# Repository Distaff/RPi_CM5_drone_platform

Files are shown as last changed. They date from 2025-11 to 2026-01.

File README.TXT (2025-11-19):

These files have been created in version 9 of KiCAD.

Some of the 3d models need to be downloaded form the following places and put into the CM5IO.3shapes directory some models are approximations.

https://datasheets.raspberrypi.org/cm5/CM5-step.zip
https://www.molex.com/molex/products/part-detail/memory_card_socket/5033981892

The models provided in the 3dmodels directory are from various manufacturers including Diodes, Hirose, MTCONN, Toby, TRXCOM. Terms and conditions for the use of the models remain with the original manufacture.

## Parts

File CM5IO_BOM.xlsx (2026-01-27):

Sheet: Bottom
Qty/ board | Ref | Value | Footprint | Desc | Part No. | MOUSER |  | Farnell |  | TME
 |  |  |  |  |  | Unit Price | Code | Unit Price | Code | Unit Price | Code | min. Il. na 10 płytek
4 | C9,C12,C13,C18 | 100n | Capacitor_SMD:C_0402_1005Metric | 0.1uF 10% 16V Ceramic Capacitor X7R 0402 (1005 Metric) | - |  |  |  |  | 0.04 zł | 04025C104KAT2A (https://www.tme.eu/pl/details/04025c104kat2a/kondensatory-mlcc-smd/kyocera-avx/) | 12 | 0.47 zł
1 | CP6 | 33pF | Capacitor_SMD:C_0805_2012Metric_Pad1.18x1.45mm_HandSolder | - | - |  |  |  |  | 0.20 zł | 08055A330KAT2A (https://www.tme.eu/pl/details/08055a330kat2a/kondensatory-mlcc-smd/kyocera-avx/) | 12 | 2.46 zł
1 | CP5 | 2.7nF | Capacitor_SMD:C_0805_2012Metric_Pad1.18x1.45mm_HandSolder | - | - |  |  |  |  | 0.18 zł | 08055C272KAT2A (https://www.tme.eu/pl/details/08055c272kat2a/kondensatory-mlcc-smd/kyocera-avx/) | 12 | 2.19 zł
1 | CP7 | 10nF | Capacitor_SMD:C_0805_2012Metric_Pad1.18x1.45mm_HandSolder | - | - |  |  |  |  | 0.14 zł | 08055C103KAT2A (https://www.tme.eu/pl/details/08055c103kat2a/kondensatory-mlcc-smd/kyocera-avx/) | 12 | 1.71 zł
1 | CP4 | 100nF | Capacitor_SMD:C_0805_2012Metric_Pad1.18x1.45mm_HandSolder | - | - |  |  |  |  | 0.04 zł | 08055C104KAT2A (https://www.tme.eu/pl/details/08055c104kat2a/kondensatory-mlcc-smd/kyocera-avx/) | 12 | 0.50 zł
4 | C2,C5,C7,C8 | 10u | Capacitor_SMD:C_0805_2012Metric | 10uF 10% 10V Ceramic Capacitor X7R 0805 (2012 Metric) | - |  |  |  |  | 0.28 zł | 08055C105KAT2A (https://www.tme.eu/pl/details/08055c105kat2a/kondensatory-mlcc-smd/kyocera-avx/) | 42 | 11.85 zł
3 | R1,R2,R10 | 1k | Resistor_SMD:R_0402_1005Metric | Resistor 1K M1005 1% 63mW | - |  |  |  |  | 0.03 zł | SMD0402-1K-1% (https://www.tme.eu/pl/details/smd0402-1k-1%25/rezystory-smd/royalohm-royal-electronic-fty-co/0402wgf1001tce/) | 100 | 3.31 zł
4 | R6,R7,R8,R9 | 2.2K 1% | Resistor_SMD:R_0402_1005Metric | Resistor 2.2K M1005 1% 63mW | - |  |  |  |  | 0.04 zł | SMD0402-2K2-1% (https://www.tme.eu/pl/details/smd0402-2k2-1%25/rezystory-smd/royalohm-royal-electronic-fty-co/0402wgf2201tce/) | 100 | 3.91 zł
2 | R11,R13 | 10K 1% | Resistor_SMD:R_0402_1005Metric | Resistor 10K M1005 1% 63mW | - |  |  |  |  | 0.02 zł | SMD0402-10K-1% (https://www.tme.eu/pl/details/smd0402-10k-1%25/rezystory-smd/royalohm-royal-electronic-fty-co/0402wgf1002tce/) | 100 | 1.76 zł
1 | R12 | 15K 1% | Resistor_SMD:R_0402_1005Metric | Resistor 15K M1005 1% 63mW | - |  |  |  |  | 0.04 zł | SMD0402-15K-1% (https://www.tme.eu/pl/details/smd0402-15k-1%25/rezystory-smd/royalohm-royal-electronic-fty-co/0402wgf1502tce/) | 100 | 3.66 zł
1 | RP1 | 115K | Resistor_SMD:R_0805_2012Metric_Pad1.20x1.40mm_HandSolder | - | - |  |  |  |  | 0.22 zł | ERA6AEB1153V (https://www.tme.eu/pl/details/era6aeb1153v/rezystory-smd/panasonic-industry-europe-gmbh/) | 12 | 2.59 zł
1 | RP2 | 22.1K | Resistor_SMD:R_0805_2012Metric_Pad1.20x1.40mm_HandSolder | - | - |  |  |  |  | 0.06 zł | SMD0805-22K1-1% (https://www.tme.eu/pl/details/smd0805-22k1-1%25/rezystory-smd/royalohm-royal-electronic-fty-co/0805s8f2212t5e/) | 100 | 5.94 zł
1 | RP3 | 15.8K | Resistor_SMD:R_0805_2012Metric_Pad1.20x1.40mm_HandSolder | - | - |  |  |  |  | 0.07 zł | SMD0805-15.8K-1% (https://www.tme.eu/pl/details/smd0805-15.8k-1%25/rezystory-smd/royalohm-royal-electronic-fty-co/0805s8f1582t5e/) | 100 | 6.71 zł
1 | J1 | POWER TERMINAL | TerminalBlock:TerminalBlock_bornier-2_P5.08mm | - | -
1 | J2 | Conn_02x06_Odd_Even | Connector_PinHeader_2.00mm:PinHeader_2x06_P2.00mm_Vertical | PinHeader_2x06_P2.54mm_Vertical | -
1 | J4 | J_PSU_EN | Connector_PinHeader_2.54mm:PinHeader_1x02_P2.54mm_Vertical | - | -
1 | J8 | THD-20-R | Connector_PinHeader_2.54mm:PinHeader_2x20_P2.54mm_Vertical | PinHeader_2x20_P2.54mm_Vertical | THD-20-R
 |  |  |  |  |  |  |  |  |  |  |  | SUMA | 47.04 zł
1 | CP1 | 10uF | Capacitor_Tantalum_SMD:CP_EIA-3528-21_Kemet-B_HandSolder | Tantalum, Kemet-B, 10uF@35V min. | - |  |  |  |  | 0.00 zł | -
2 | CP2,CP3 | 22uF | Capacitor_Tantalum_SMD:CP_EIA-3528-21_Kemet-B_HandSolder | Tantalum, Kemet-B, 22uF@10V min. | - |  |  |  |  | 1.64 zł | TAJB226K016R (https://www.tme.eu/pl/details/tajb226k016r/kondensatory-tantalowe-smd/kyocera-avx/tajb226k016rnj/)
1 | C3 | 100uF | Capacitor_Tantalum_SMD:CP_EIA-7343-31_Kemet-D | Kemet-D, 10V | - |  |  |  |  | 2.28 zł | TAJD106K035R (https://www.tme.eu/pl/details/tajd106k035r/kondensatory-tantalowe-smd/kyocera-avx/tajd106k035rnj/)
2 | D1,D3 | LED Red | LED_SMD:LED_0603_1608Metric | Red 620nm LED Indication - Discrete 2.2V 2-SMD, No Lead | SML-A12U8TT86Q |  |  | 1.65 zł | 3434715 (https://pl.farnell.com/rohm/sml-a12u8tt86/led-red-63mcd-620nm/dp/3434715) | 0.00 zł | -
1 | D2 | LED Green | LED_SMD:LED_0603_1608Metric | Green 572nm LED Indication - Discrete 2.2V 2-SMD, No Lead | SML-A12M8TT86N |  |  | 1.64 zł | 3434712 (https://pl.farnell.com/rohm/sml-a12m8tt86/led-yellow-green-25mcd-572nm/dp/3434712) | 0.00 zł | -
2 | J5,J16 | Conn_01x22_Female | CM5IO:Hirose_FH12-22S-0.5SH_1x22-1MP_P0.50mm_Horizontal | 22 Position FFC, FPC Connector Contacts, Bottom 0.020" (0.50mm) Surface Mount, Right Angle | FH12-22S-0.5SH55 |  |  | 7.17 zł | 2300373 (https://pl.farnell.com/hirose-hrs/fh12-22s-1sh-55/connector-fpc-ffc-smt-1mm-22way/dp/2300373) | 0.00 zł | -
1 | J7 | Micro_SD_Card_Det | CM5IO:SDCARD_MOLEX_503398-1892 | 9 (8 + 1) Position Card Connector microSDâ„¢ Surface Mount, Right Angle Gold | 503398-1892 |  |  |  |  | 8.41 zł | MX-503398-1892 (https://www.tme.eu/pl/details/mx-503398-1892/zlacza-do-kart/molex-interconnect-gmbh/503398-1892/) | Not necessary, if no SD card is used
1 | J11 | USB_C_Receptacle_USB2.0 | Connector_USB:USB_C_Receptacle_GCT_USB4105-xx-A_16P_TopMnt_Horizontal | USBC USB2 data and power connector | USBF31-0171 |  |  |  |  | 2.58 zł | UBC-RA-TF* (https://www.tme.eu/pl/details/ubc-ra-tf/zlacza-usb-i-ieee1394/jst-j-s-t-deutschland-gmbh/ubc-ra-tf-hf/) | * - equivalent
1 | J12 | USB3_A | Connector_USB:USB3_A_Molex_48393-001 | USB 3.0 A connector | 48393-0003 |  |  |  |  | 9.67 zł | MX-48393-0003 (https://www.tme.eu/pl/details/mx-48393-0003/zlacza-usb-i-ieee1394/molex-interconnect-gmbh/48393-0003/)
1 | J14 | JST_SHBM04B-SRSS-TB | Connector_JST:JST_SH_BM04B-SRSS-TB_1x04-1MP_P1.00mm_Vertical | 4 pin vertical 1mm pitch connector | SHBM04B-SRSS-TB |  |  |  |  | 1.44 zł | SM04B-SRSS-TB (https://www.tme.eu/pl/details/sm04b-srss-tb/zlacza-sygnalowe-raster-1-00mm/jst-j-s-t-deutschland-gmbh/sm04b-srss-tb-lf-sn/)
1 | J22 | 46765-1301 | CM5IO:CONN_467651301_MOL | 0.40mm Pitch Micro HDMI Connector, Right-Angle Receptacle, Surface Mount, with Through Hole Shell Tabs and Pick-and-Place Polyimide Tape, 19 Circuits, Lead-Free | 46765-1301 |  |  | 8.82 zł | 2614867 (https://pl.farnell.com/molex/46765-1301/hdmi-connector-rcpt-19pos-smt/dp/2614867) | 0.00 zł | -
1 | LP1 | 3.6uH | Inductor_SMD:L_Bourns-SRN8040_8x8.15mm | - | SRN8040HA-3R6M |  |  | 2.52 zł | 4216300 (https://pl.farnell.com/bourns/srn8040ha-3r6m/power-inductor-3-6uh-semishielded/dp/4216300) | 0.00 zł | -
2 | Module1 | ComputeModule5-CM5 | CM5IO:Raspberry-Pi-5-Compute-Module | 100 Position Connector Receptacle, Center Strip Contacts Surface Mount Gold | 10164227-1001A1RLF | 0.00 zł | - | 7.43 zł | 4137104 (https://pl.farnell.com/amphenol-communications-solutions/10164227-1001a1rlf/mezzanine-conn-rcpt-100pos-2row/dp/4137104) | 0.00 zł | -
1 | SW1 | Right angle Tact button | Button_Switch_SMD:SW_Push_1P1T_NO_CK_KMR2 | - | KMR221G LFS |  |  |  |  | 1.05 zł | KMR221GLFS (https://www.tme.eu/pl/details/kmr221glfs/mikroprzelaczniki-tact/c-k-components-sas/kmr221g-lfs/)
1 | U6 | AP22653W6 | Package_TO_SOT_SMD:SOT-23-6 | Power Switch/Driver 1:1 P-Channel 2.1A SOT-23-6 | AP22653W6 |  |  |  |  | 1.45 zł | AP22653W6-7 (https://www.tme.eu/pl/details/ap22653w6-7/power-switches-uklady-scalone/diodes-incorporated/)
1 | U12 | RT9742SNGV | Package_TO_SOT_SMD:TSOT-23_HandSoldering | Power Switch/Driver 1:1 N-Channel 500mA SOT-23-3 | RT9742SNGV |  |  | 1.50 zł | 2575555 (https://pl.farnell.com/richtek/rt9742sngv/uswi00154-rt9742sngv/dp/2575555) | 0.00 zł | -
1 | U18 | RT9742GGJ5 | Package_TO_SOT_SMD:SOT-23-5 | Power Switch/Driver 1:1 N-Channel 1A TSOT-23-5 | RT9742GGJ5 |  |  | 0.00 zł | - | 0.00 zł | - | Not necessary, if no SD card is used
1 | UP1 | AP64501SP-13 | CM5IO:SOP_AP64501SP-13_DIO | - | AP64501SP-13 |  |  |  |  | 7.11 zł | AP64501SP-13 (https://www.tme.eu/pl/details/ap64501sp-13/regulatory-napiecia-uklady-dc-dc/diodes-incorporated/)
 |  |  |  |  |  |  |  | 46.98 zł | SUMA / płytka | 37.27 zł | SUMA / płytka

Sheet: Top
Qty/ board | Ref | Value | Footprint | Desc | Part No. | MOUSER |  | Farnell |  | TME
 |  |  |  |  |  | Unit Price | Code | Unit Price | Code | Unit Price | Code | min. Il. na 10 płytek
1 | J8 | THD-20-R | Connector_PinHeader_2.54mm:PinHeader_2x20_P2.54mm_Vertical | TODO: to ma być gniazdo | - |  |  |  |  |  |  |  | 0.00 zł
1 | J3 | J_PSU_EN | Connector_PinHeader_2.54mm:PinHeader_1x02_P2.54mm_Vertical_SMD_Pin1Left | - | - |  |  |  |  |  |  |  | 0.00 zł
4 | C1,C2,C7,C8 | 470nF | Capacitor_SMD:C_0805_2012Metric_Pad1.18x1.45mm_HandSolder | - | - |  |  |  |  | 0.25 zł | 08055C474K4T2A (https://www.tme.eu/pl/details/08055c474k4t2a/kondensatory-mlcc-smd/kyocera-avx/) | 50 | 12.36 zł
10 | R1,R3,R4,R5,R6,R9,R10,R12,R13,R15 | 1K | Resistor_SMD:R_0805_2012Metric_Pad1.20x1.40mm_HandSolder | - | - |  |  |  |  | 0.05 zł | SMD0805-1K-1% (https://www.tme.eu/pl/details/smd0805-1k-1%25/rezystory-smd/royalohm-royal-electronic-fty-co/0805s8f1001t5e/) | 100 | 4.97 zł
1 | R2 | 2.2K 1% | Resistor_SMD:R_0805_2012Metric_Pad1.20x1.40mm_HandSolder | - | - |  |  |  |  | 0.06 zł | SMD0805-2K2-1% (https://www.tme.eu/pl/details/smd0805-2k2-1%25/rezystory-smd/royalohm-royal-electronic-fty-co/0805s8f2201t5e/) | 100 | 5.62 zł
2 | R7,R8 | 5.1K 1% | Resistor_SMD:R_0805_2012Metric_Pad1.20x1.40mm_HandSolder | - | - |  |  |  |  | 0.06 zł | SMD0805-5K1-1% (https://www.tme.eu/pl/details/smd0805-5k1-1%25/rezystory-smd/royalohm-royal-electronic-fty-co/0805s8f5101t5e/) | 100 | 5.94 zł
3 | R11,R14,R16 | 10K | Resistor_SMD:R_0805_2012Metric_Pad1.20x1.40mm_HandSolder | - | - |  |  |  |  | 0.05 zł | SMD0805-10K-1% (https://www.tme.eu/pl/details/smd0805-10k-1%25/rezystory-smd/royalohm-royal-electronic-fty-co/0805s8f1002t5e/) | 100 | 4.97 zł
 |  |  |  |  |  |  |  |  |  |  |  | SUMA/całość | 33.85 zł
2 | C3,C4 | 4.7uF 35v | Capacitor_Tantalum_SMD:CP_EIA-3528-21_Kemet-B_HandSolder | - | - |  |  |  |  | 1.68 zł | TAJB475K035R (https://www.tme.eu/pl/details/tajb475k035r/kondensatory-tantalowe-smd/kyocera-avx/tajb475k035rnj/)
2 | C5,C6 | 4.7uF 10v | Capacitor_Tantalum_SMD:CP_EIA-3216-18_Kemet-A_HandSolder | - | - |  |  |  |  | 1.48 zł | TAJA475K010R (https://www.tme.eu/pl/details/taja475k010r/kondensatory-tantalowe-smd/kyocera-avx/taja475k010rnj/)
2 | D1,D2 | MBR1020VL | Diode_SMD:D_SOD-123F | - | MBR1020VL |  |  |  |  | 0.98 zł | MBR1020VL-AU-R1 (https://www.tme.eu/pl/details/mbr1020vl-au-r1/diody-schottky-smd/panjit-semiconductor-panjit-international-inc/mbr1020vl-au-r1-000a1/)
2 | D3,D5 | LED Red | LED_SMD:LED_0603_1608Metric | Red 620nm LED Indication - Discrete 2.2V 2-SMD, No Lead | SML-A12U8TT86Q |  |  |  |  | 0.15 zł | LTST-C190KRKT* (https://www.tme.eu/pl/details/ltst-c190krkt/diody-led-smd-kolorowe/lite-on-technology/) | * - equivalent
1 | D4 | LED Green | LED_SMD:LED_0603_1608Metric | Green 572nm LED Indication - Discrete 2.2V 2-SMD, No Lead | SML-A12M8TT86N |  |  |  |  | 0.12 zł | LTST-C190KGKT* (https://www.tme.eu/pl/details/ltst-c190kgkt/diody-led-smd-kolorowe/lite-on-technology/)
1 | J1 | USB_C_Receptacle_USB2.0 | Connector_USB:USB_C_Receptacle_GCT_USB4105-xx-A_16P_TopMnt_Horizontal | - |  |  |  |  |  | 2.58 zł | UBC-RA-TF (https://www.tme.eu/pl/details/ubc-ra-tf/zlacza-usb-i-ieee1394/jst-j-s-t-deutschland-gmbh/ubc-ra-tf-hf/)
1 | J4 | J_ESP_DBG_UART | Connector_Molex:Molex_PicoBlade_53047-0210_1x02_P1.25mm_Vertical | - | 53047-0210 |  |  |  |  | 0.90 zł | MX-53047-0210 (https://www.tme.eu/pl/details/mx-53047-0210/zlacza-sygnalowe-raster-1-25mm/molex-interconnect-gmbh/53047-0210/)
1 | J7 | J_FC_UART | Connector_Molex:Molex_PicoBlade_53048-0210_1x02_P1.25mm_Horizontal | - | 53048-0210 |  |  |  |  | 0.93 zł | MX-53048-0210 (https://www.tme.eu/pl/details/mx-53048-0210/zlacza-sygnalowe-raster-1-25mm/molex-interconnect-gmbh/53048-0210/)
2 | J9,J10 |  | Connector_Molex:Molex_PicoBlade_53048-0810_1x08_P1.25mm_Horizontal | - | 53048-0810 |  |  |  |  | 2.25 zł | MX-53048-0810 (https://www.tme.eu/pl/details/mx-53048-0810/zlacza-sygnalowe-raster-1-25mm/molex-interconnect-gmbh/53048-0810/)
2 | Q1,Q4 | AO3401A | Package_TO_SOT_SMD:SOT-23 | - | AO3401A |  |  |  |  | 1.24 zł | AO3401A (https://www.tme.eu/pl/details/ao3401a/tranzystory-z-kanalem-p-smd/alpha-omega-semiconductor-inc/)
2 | Q2,Q3 | Q_NPN_BEC | Package_TO_SOT_SMD:SOT-23 | -
3 | SW1,SW2,SW3 |  | Button_Switch_SMD:SW_Push_1P1T_NO_CK_KMR2 | - | KMR221G LFS |  |  |  |  | 1.05 zł | KMR221GLFS (https://www.tme.eu/pl/details/kmr221glfs/mikroprzelaczniki-tact/c-k-components-sas/kmr221g-lfs/)
1 | U1 | ESP32-S3-WROOM-1 | RF_Module:ESP32-S3-WROOM-1U | - | ESP32-S3-WROOM-1 |  |  |  |  | 23.40 zł | ESP32S3-WRM1U-16R8 (https://www.tme.eu/pl/details/esp32s3-wrm1u-16r8/moduly-iot-wifi-bluetooth/espressif-systems/esp32-s3-wroom-1u-n16r8/)
1 | U2 | Wio-SX1262 | CM5IO_top:Wio-SX1262 | - | Seed Studio 114993390 |  |  |  |  | 0.00 zł | -
2 | U3,U4 | AP7361C-33E | Package_TO_SOT_SMD:SOT-223-3_TabPin2 | - | AP7361C-33E |  |  |  |  | 1.53 zł | AP7361C-33E-13 (https://www.tme.eu/pl/details/ap7361c-33e-13/stabilizatory-napiecia-nieregulowane-ldo/diodes-incorporated/)
 |  |  |  |  |  |  |  |  |  | 49.70 zł | SUMA / płytka

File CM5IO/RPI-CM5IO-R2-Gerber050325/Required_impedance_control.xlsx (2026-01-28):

Signal Layer | Reference Layer | Impedance Type | Trace Width（mil) | Trace Spacing（mil) | Impedance(ohm)±10% | Position
L1 | L2 | Differential Pair (Non coplanar) | 4.25 | 5.9055 | 100
L4 | L3 | Differential Pair (Non coplanar) | 4.25 | 5.9055 | 100
L1 | L2 | Differential Pair (Non coplanar) | 6.6 | 9.9606 | 90
L4 | L3 | Differential Pair (Non coplanar) | 6.6 | 9.9606 | 90

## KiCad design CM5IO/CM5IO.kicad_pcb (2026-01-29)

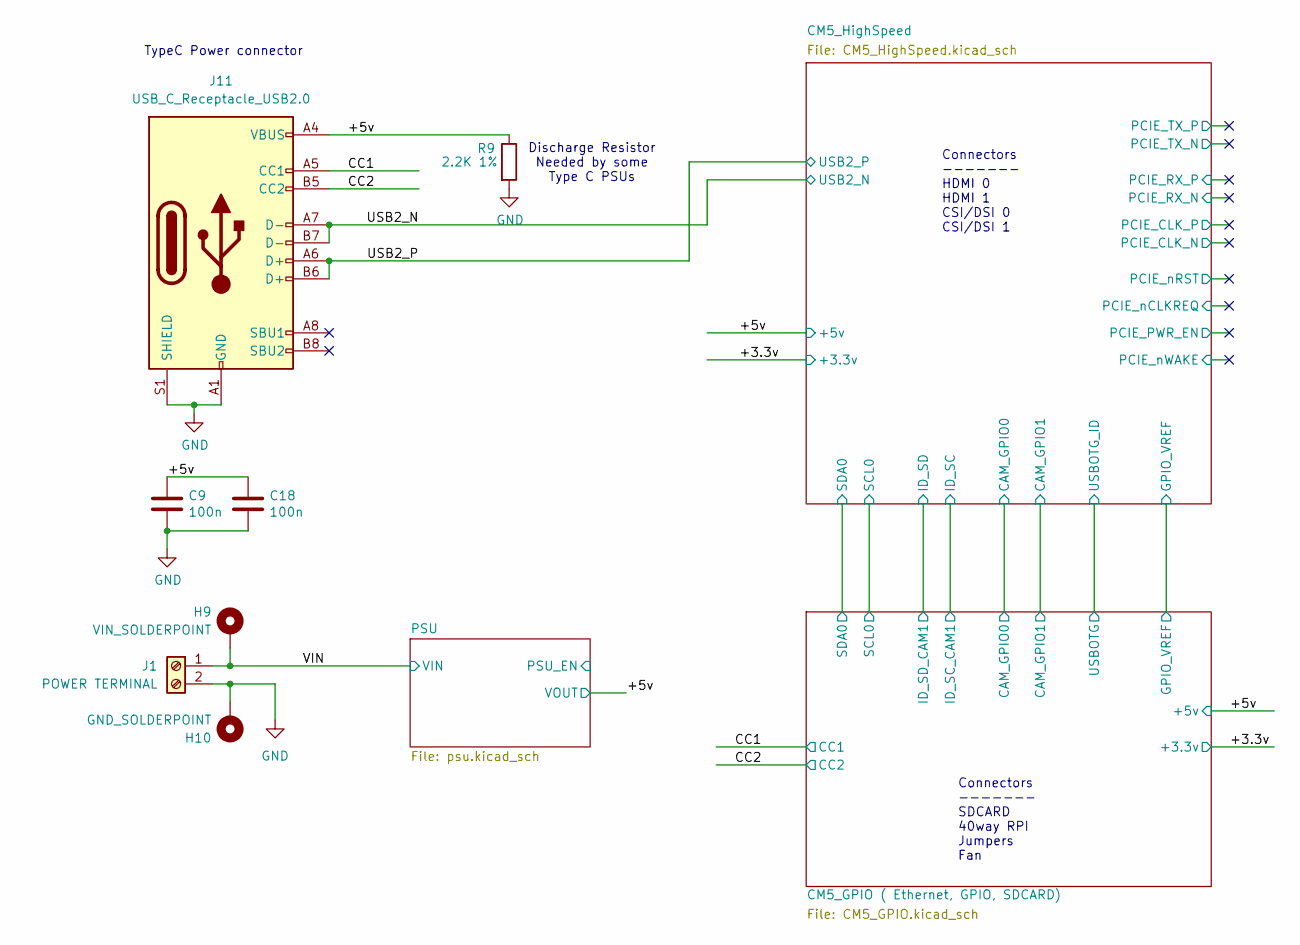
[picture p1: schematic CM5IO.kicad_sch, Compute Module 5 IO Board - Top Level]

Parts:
C9, C18: 100n; C_0402_1005Metric; Part Description 0.1uF 10% 16V Ceramic Capacitor X7R 040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
H9: VIN_SOLDERPOINT; SolderWirePad_1x01_SMD_5x10mm
H10: GND_SOLDERPOINT; SolderWirePad_1x01_SMD_5x10mm
J1: POWER TERMINAL; TerminalBlock_bornier-2_P5.08mm
J11: USB_C_Receptacle_USB2.0; USB_C_Receptacle_GCT_USB4105-xx-A_16P_TopMnt_Horizontal; Part Description USBC USB2 data and power connector
R9: 2.2K 1%; R_0402_1005Metric; Part Description Resistor 2.2K M1005 1% 63mW

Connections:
/+5v: C9.1, C18.1, J11.A4 (VBUS), J11.A9 (VBUS), J11.B4 (VBUS), J11.B9 (VBUS), R9.1; also elsewhere on the board
/CC1: J11.A5 (CC1); also elsewhere on the board
/CC2: J11.B5 (CC2); also elsewhere on the board
/USB2_N: J11.A7 (D-), J11.B7 (D-); also elsewhere on the board
/USB2_P: J11.A6 (D+), J11.B6 (D+); also elsewhere on the board
/VIN: H9.1 (MP), J1.1; also elsewhere on the board
GND: C9.2, C18.2, H10.1 (MP), J1.2, J11.A1 (GND), J11.A12 (GND), J11.B1 (GND), J11.B12 (GND), J11.S1 (SHIELD), R9.2; also elsewhere on the board

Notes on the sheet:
Connectors ------- SDCARD 40way RPI Jumpers Fan
Discharge Resistor Needed by some Type C PSUs
TypeC Power connector
Connectors ------- HDMI 0 HDMI 1 CSI/DSI 0 CSI/DSI 1

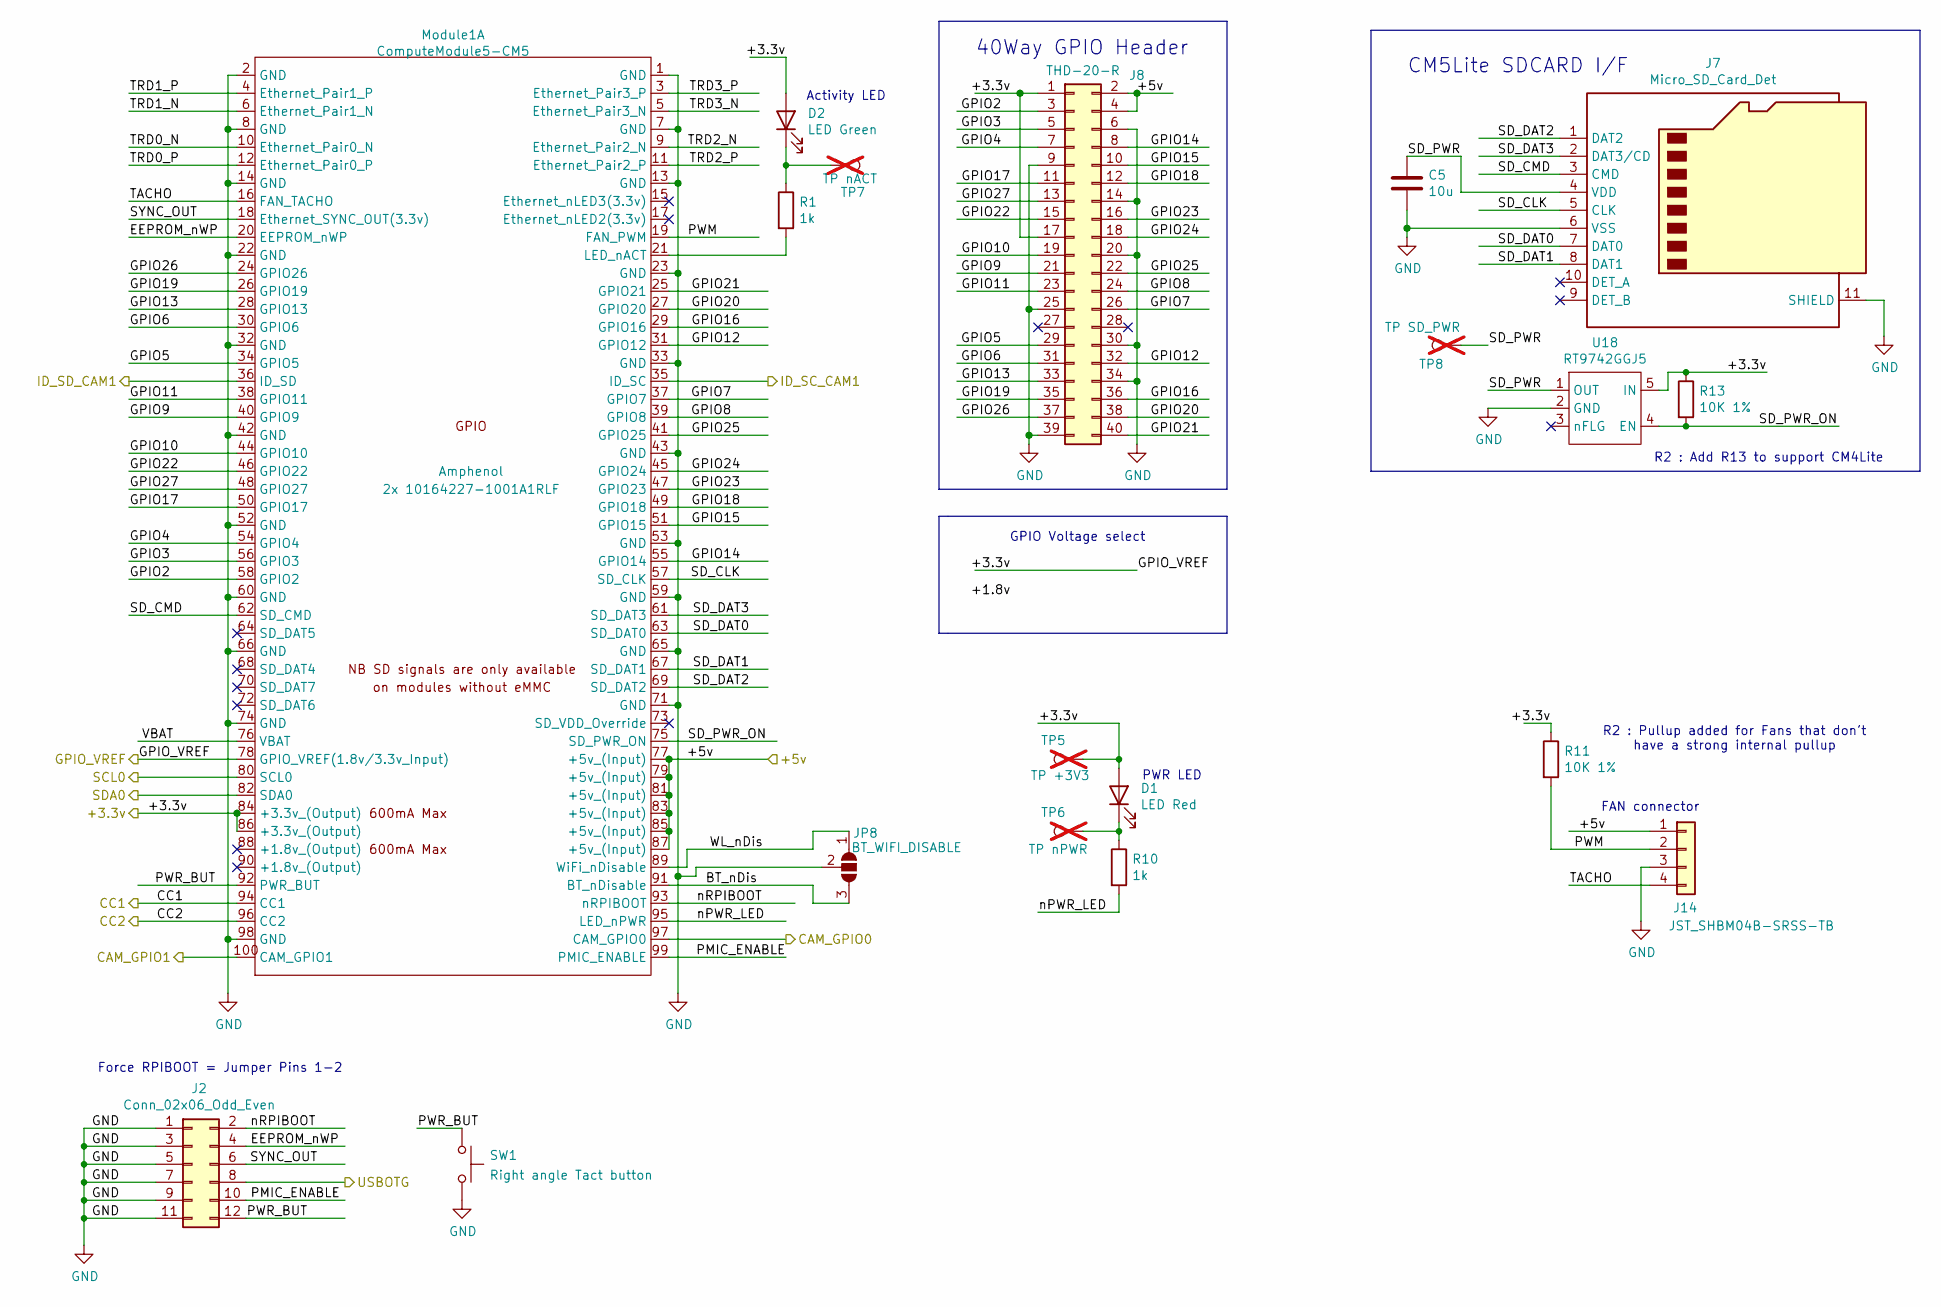
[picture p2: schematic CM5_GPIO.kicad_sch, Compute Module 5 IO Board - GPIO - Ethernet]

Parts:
C5: 10u; C_0805_2012Metric; Part Description 10uF 10% 10V Ceramic Capacitor X7R 0805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
D1: LED Red; LED_0603_1608Metric; Part Description Red 620nm LED Indication - Discrete 2.2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
D2: LED Green; LED_0603_1608Metric; Part Description Green 572nm LED Indication - Discrete 2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
J2: Conn_02x06_Odd_Even; PinHeader_2x06_P2.00mm_Vertical; Part Description PinHeader_2x06_P2.54mm_Vertical
J7: Micro_SD_Card_Det; SDCARD_MOLEX_503398-1892; Part Description 9 (8 + 1) Position Card Connector micro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
J8: THD-20-R; PinHeader_2x20_P2.54mm_Vertical; Part Description PinHeader_2x20_P2.54mm_Vertical
J14: JST_SHBM04B-SRSS-TB; JST_SH_BM04B-SRSS-TB_1x04-1MP_P1.00mm_Vertical; Part Description 4 pin vertical 1mm pitch connector
JP8: BT_WIFI_DISABLE; SolderJumper-3_P2.0mm_Open_TrianglePad1.0x1.5mm
Module1: ComputeModule5-CM5; Raspberry-Pi-5-Compute-Module; Part Description 100 Position Connector Receptacle, Cent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
R1, R10: 1k; R_0402_1005Metric; Part Description Resistor 1K M1005 1% 63mW
R11, R13: 10K 1%; R_0402_1005Metric; Part Description Resistor 10K M1005 1% 63mW
SW1: Right angle Tact button; SW_Push_1P1T_NO_CK_KMR2
TP5: TP +3V3; TestPoint_Pad_2.0x2.0mm; Part Description Test point; not fitted
TP6: TP nPWR; TestPoint_Pad_2.0x2.0mm; Part Description Test point; not fitted
TP7: TP nACT; TestPoint_Pad_2.0x2.0mm; Part Description Test point; not fitted
TP8: TP SD_PWR; TestPoint_Pad_2.0x2.0mm; Part Description Test point; not fitted
U18: RT9742GGJ5; SOT-23-5; Part Description Power Switch/Driver 1:1 N-Channel 1A TS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

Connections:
/+3.3v: D1.2 (A), D2.2 (A), J8.1, J8.17, Module1.78 (GPIO_VREF(1.8v/3.3v_Input)), Module1.84 (+3.3v_(Output)), Module1.86 (+3.3v_(Output)), R11.1, R13.1, TP5.1, U18.5 (IN); also elsewhere on the board
/+5v: J8.2, J8.4, J14.1, Module1.77 (+5v_(Input)), Module1.79 (+5v_(Input)), Module1.81 (+5v_(Input)), Module1.83 (+5v_(Input)), Module1.85 (+5v_(Input)), Module1.87 (+5v_(Input)); also elsewhere on the board
/CC1: Module1.94 (CC1); also elsewhere on the board
/CC2: Module1.96 (CC2); also elsewhere on the board
/CM5_GPIO ( Ethernet, GPIO, SDCARD)/BT_nDis: JP8.3 (B), Module1.91 (BT_nDisable)
/CM5_GPIO ( Ethernet, GPIO, SDCARD)/CAM_GPIO0: Module1.97 (CAM_GPIO0); also elsewhere on the board
/CM5_GPIO ( Ethernet, GPIO, SDCARD)/CAM_GPIO1: Module1.100 (CAM_GPIO1); also elsewhere on the board
/CM5_GPIO ( Ethernet, GPIO, SDCARD)/EEPROM_nWP: J2.4, Module1.20 (EEPROM_nWP)
/CM5_GPIO ( Ethernet, GPIO, SDCARD)/GPIO2: J8.3, Module1.58 (GPIO2)
/CM5_GPIO ( Ethernet, GPIO, SDCARD)/GPIO3: J8.5, Module1.56 (GPIO3)
/CM5_GPIO ( Ethernet, GPIO, SDCARD)/GPIO4: J8.7, Module1.54 (GPIO4)
/CM5_GPIO ( Ethernet, GPIO, SDCARD)/GPIO5: J8.29, Module1.34 (GPIO5)
/CM5_GPIO ( Ethernet, GPIO, SDCARD)/GPIO6: J8.31, Module1.30 (GPIO6)
/CM5_GPIO ( Ethernet, GPIO, SDCARD)/GPIO7: J8.26, Module1.37 (GPIO7)
/CM5_GPIO ( Ethernet, GPIO, SDCARD)/GPIO8: J8.24, Module1.39 (GPIO8)
/CM5_GPIO ( Ethernet, GPIO, SDCARD)/GPIO9: J8.21, Module1.40 (GPIO9)
/CM5_GPIO ( Ethernet, GPIO, SDCARD)/GPIO10: J8.19, Module1.44 (GPIO10)
/CM5_GPIO ( Ethernet, GPIO, SDCARD)/GPIO11: J8.23, Module1.38 (GPIO11)
/CM5_GPIO ( Ethernet, GPIO, SDCARD)/GPIO12: J8.32, Module1.31 (GPIO12)
/CM5_GPIO ( Ethernet, GPIO, SDCARD)/GPIO13: J8.33, Module1.28 (GPIO13)
/CM5_GPIO ( Ethernet, GPIO, SDCARD)/GPIO14: J8.8, Module1.55 (GPIO14)
/CM5_GPIO ( Ethernet, GPIO, SDCARD)/GPIO15: J8.10, Module1.51 (GPIO15)
/CM5_GPIO ( Ethernet, GPIO, SDCARD)/GPIO16: J8.36, Module1.29 (GPIO16)
/CM5_GPIO ( Ethernet, GPIO, SDCARD)/GPIO17: J8.11, Module1.50 (GPIO17)
/CM5_GPIO ( Ethernet, GPIO, SDCARD)/GPIO18: J8.12, Module1.49 (GPIO18)
/CM5_GPIO ( Ethernet, GPIO, SDCARD)/GPIO19: J8.35, Module1.26 (GPIO19)
/CM5_GPIO ( Ethernet, GPIO, SDCARD)/GPIO20: J8.38, Module1.27 (GPIO20)
/CM5_GPIO ( Ethernet, GPIO, SDCARD)/GPIO21: J8.40, Module1.25 (GPIO21)
/CM5_GPIO ( Ethernet, GPIO, SDCARD)/GPIO22: J8.15, Module1.46 (GPIO22)
/CM5_GPIO ( Ethernet, GPIO, SDCARD)/GPIO23: J8.16, Module1.47 (GPIO23)
/CM5_GPIO ( Ethernet, GPIO, SDCARD)/GPIO24: J8.18, Module1.45 (GPIO24)
/CM5_GPIO ( Ethernet, GPIO, SDCARD)/GPIO25: J8.22, Module1.41 (GPIO25)
/CM5_GPIO ( Ethernet, GPIO, SDCARD)/GPIO26: J8.37, Module1.24 (GPIO26)
/CM5_GPIO ( Ethernet, GPIO, SDCARD)/GPIO27: J8.13, Module1.48 (GPIO27)
/CM5_GPIO ( Ethernet, GPIO, SDCARD)/PMIC_ENABLE: J2.10, Module1.99 (PMIC_ENABLE)
/CM5_GPIO ( Ethernet, GPIO, SDCARD)/PWM: J14.2, Module1.19 (FAN_PWM), R11.2
/CM5_GPIO ( Ethernet, GPIO, SDCARD)/PWR_BUT: J2.12, Module1.92 (PWR_BUT), SW1.1
/CM5_GPIO ( Ethernet, GPIO, SDCARD)/SD_CLK: J7.5 (CLK), Module1.57 (SD_CLK)
/CM5_GPIO ( Ethernet, GPIO, SDCARD)/SD_CMD: J7.3 (CMD), Module1.62 (SD_CMD)
/CM5_GPIO ( Ethernet, GPIO, SDCARD)/SD_DAT0: J7.7 (DAT0), Module1.63 (SD_DAT0)
/CM5_GPIO ( Ethernet, GPIO, SDCARD)/SD_DAT1: J7.8 (DAT1), Module1.67 (SD_DAT1)
/CM5_GPIO ( Ethernet, GPIO, SDCARD)/SD_DAT2: J7.1 (DAT2), Module1.69 (SD_DAT2)
/CM5_GPIO ( Ethernet, GPIO, SDCARD)/SD_DAT3: J7.2 (DAT3/CD), Module1.61 (SD_DAT3)
/CM5_GPIO ( Ethernet, GPIO, SDCARD)/SD_PWR: C5.1, J7.4 (VDD), TP8.1, U18.1 (OUT)
/CM5_GPIO ( Ethernet, GPIO, SDCARD)/SD_PWR_ON: Module1.75 (SD_PWR_ON), R13.2, U18.4 (EN)
/CM5_GPIO ( Ethernet, GPIO, SDCARD)/SYNC_OUT: J2.6, Module1.18 (Ethernet_SYNC_OUT(3.3v))
/CM5_GPIO ( Ethernet, GPIO, SDCARD)/TACHO: J14.4, Module1.16 (FAN_TACHO)
/CM5_GPIO ( Ethernet, GPIO, SDCARD)/TRD0_N: Module1.10 (Ethernet_Pair0_N)
/CM5_GPIO ( Ethernet, GPIO, SDCARD)/TRD0_P: Module1.12 (Ethernet_Pair0_P)
/CM5_GPIO ( Ethernet, GPIO, SDCARD)/TRD1_N: Module1.6 (Ethernet_Pair1_N)
/CM5_GPIO ( Ethernet, GPIO, SDCARD)/TRD1_P: Module1.4 (Ethernet_Pair1_P)
/CM5_GPIO ( Ethernet, GPIO, SDCARD)/TRD2_N: Module1.9 (Ethernet_Pair2_N)
/CM5_GPIO ( Ethernet, GPIO, SDCARD)/TRD2_P: Module1.11 (Ethernet_Pair2_P)
/CM5_GPIO ( Ethernet, GPIO, SDCARD)/TRD3_N: Module1.5 (Ethernet_Pair3_N)
/CM5_GPIO ( Ethernet, GPIO, SDCARD)/TRD3_P: Module1.3 (Ethernet_Pair3_P)
/CM5_GPIO ( Ethernet, GPIO, SDCARD)/USBOTG: J2.8; also elsewhere on the board
/CM5_GPIO ( Ethernet, GPIO, SDCARD)/VBAT: Module1.76 (VBAT)
/CM5_GPIO ( Ethernet, GPIO, SDCARD)/WL_nDis: JP8.1 (A), Module1.89 (WiFi_nDisable)
/CM5_GPIO ( Ethernet, GPIO, SDCARD)/nPWR_LED: Module1.95 (LED_nPWR), R10.2
/CM5_GPIO ( Ethernet, GPIO, SDCARD)/nRPIBOOT: J2.2, Module1.93 (nRPIBOOT)
/CM5_HighSpeed/SCL0: Module1.80 (SCL0); also elsewhere on the board
/CM5_HighSpeed/SCL1: Module1.35 (ID_SC); also elsewhere on the board
/CM5_HighSpeed/SDA0: Module1.82 (SDA0); also elsewhere on the board
/CM5_HighSpeed/SDA1: Module1.36 (ID_SD); also elsewhere on the board
GND: C5.2, J2.1, J2.3, J2.5, J2.7, J2.9, J2.11, J7.6 (VSS), J7.11 (SHIELD), J8.6, J8.9, J8.14, J8.20, J8.25, J8.30, J8.34, J8.39, J14.3, JP8.2 (C), Module1.1 (GND), Module1.2 (GND), Module1.7 (GND), Module1.8 (GND), Module1.13 (GND), Module1.14 (GND), Module1.22 (GND), Module1.23 (GND), Module1.32 (GND), Module1.33 (GND), Module1.42 (GND), Module1.43 (GND), Module1.52 (GND), Module1.53 (GND), Module1.59 (GND), Module1.60 (GND), Module1.65 (GND), Module1.66 (GND), Module1.71 (GND), Module1.74 (GND), Module1.98 (GND), SW1.2, U18.2 (GND); also elsewhere on the board
unnamed: D1.1 (K), R10.1, TP6.1
unnamed: D2.1 (K), R1.1, TP7.1
unnamed: Module1.21 (LED_nACT), R1.2

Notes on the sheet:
40Way GPIO Header
R2 : Pullup added for Fans that don't have a strong internal pullup
Activity LED
R2 : Add R13 to support CM4Lite
GPIO Voltage select
Force RPIBOOT = Jumper Pins 1-2
PWR LED
FAN connector
CM5Lite SDCARD I/F

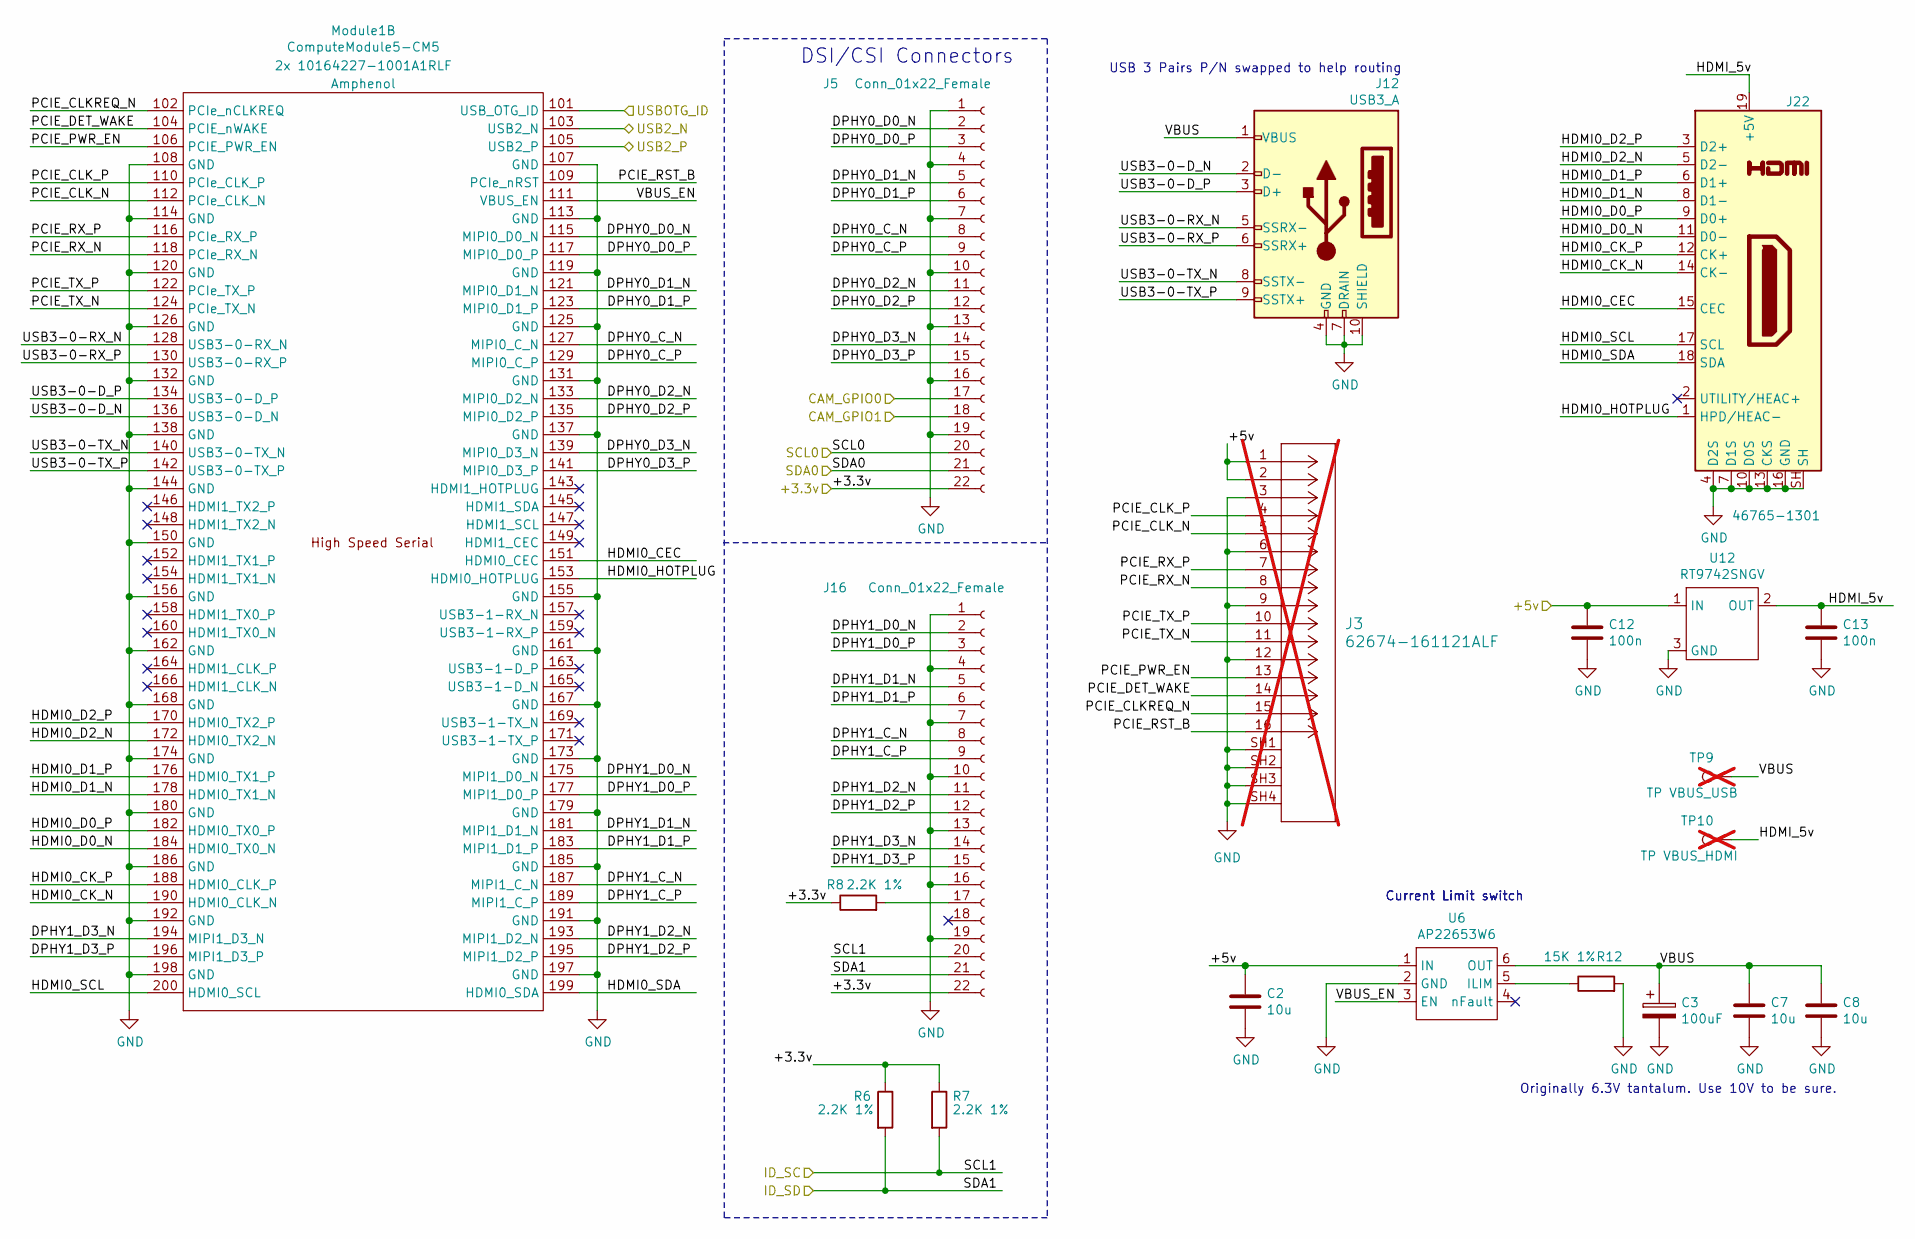
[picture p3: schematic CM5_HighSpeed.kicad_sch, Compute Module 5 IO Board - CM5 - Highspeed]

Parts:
C2, C7, C8: 10u; C_0805_2012Metric; Part Description 10uF 10% 10V Ceramic Capacitor X7R 0805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
C3: 100uF; CP_EIA-7343-31_Kemet-D; Part Description Capacitor, SP-Cap, 100u, 6.3V, 15mR ESR
C12, C13: 100n; C_0402_1005Metric; Part Description 0.1uF 10% 16V Ceramic Capacitor X7R 040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
J3: 62674-161121ALF; CON16_1X16_DUT_58XF_GLE; not fitted
J5, J16: Conn_01x22_Female; Hirose_FH12-22S-0.5SH_1x22-1MP_P0.50mm_Horizontal; Part Description 22 Position FFC, FPC Connector Contacts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
J12: USB3_A; USB3_A_Molex_48393-001; Part Description USB 3.0 A connector
J22: 46765-1301; CONN_467651301_MOL; Part Description 0.40mm Pitch Micro HDMI Connector, Righ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
Module1: ComputeModule5-CM5; Raspberry-Pi-5-Compute-Module; Part Description 100 Position Connector Receptacle, Cent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
R6, R7, R8: 2.2K 1%; R_0402_1005Metric; Part Description Resistor 2.2K M1005 1% 63mW
R12: 15K 1%; R_0402_1005Metric; Part Description Resistor 15K M1005 1% 63mW
TP9: TP VBUS_USB; TestPoint_Pad_2.0x2.0mm; Part Description Test point; not fitted
TP10: TP VBUS_HDMI; TestPoint_Pad_2.0x2.0mm; Part Description Test point; not fitted
U6: AP22653W6; SOT-23-6; Part Description Power Switch/Driver 1:1 P-Channel 2.1A 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
U12: RT9742SNGV; TSOT-23_HandSoldering; Part Description Power Switch/Driver 1:1 N-Channel 500mA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

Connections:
/+3.3v: J5.22, J16.22, R6.1, R7.1, R8.1; also elsewhere on the board
/+5v: C2.1, C12.1, J3.1, J3.2, U6.1 (IN), U12.1 (IN); also elsewhere on the board
/CM5_GPIO ( Ethernet, GPIO, SDCARD)/CAM_GPIO0: J5.17; also elsewhere on the board
/CM5_GPIO ( Ethernet, GPIO, SDCARD)/CAM_GPIO1: J5.18; also elsewhere on the board
/CM5_GPIO ( Ethernet, GPIO, SDCARD)/USBOTG: Module1.101 (USB_OTG_ID); also elsewhere on the board
/CM5_HighSpeed/DPHY0_C_N: J5.8, Module1.127 (MIPI0_C_N)
/CM5_HighSpeed/DPHY0_C_P: J5.9, Module1.129 (MIPI0_C_P)
/CM5_HighSpeed/DPHY0_D0_N: J5.2, Module1.115 (MIPI0_D0_N)
/CM5_HighSpeed/DPHY0_D0_P: J5.3, Module1.117 (MIPI0_D0_P)
/CM5_HighSpeed/DPHY0_D1_N: J5.5, Module1.121 (MIPI0_D1_N)
/CM5_HighSpeed/DPHY0_D1_P: J5.6, Module1.123 (MIPI0_D1_P)
/CM5_HighSpeed/DPHY0_D2_N: J5.11, Module1.133 (MIPI0_D2_N)
/CM5_HighSpeed/DPHY0_D2_P: J5.12, Module1.135 (MIPI0_D2_P)
/CM5_HighSpeed/DPHY0_D3_N: J5.14, Module1.139 (MIPI0_D3_N)
/CM5_HighSpeed/DPHY0_D3_P: J5.15, Module1.141 (MIPI0_D3_P)
/CM5_HighSpeed/DPHY1_C_N: J16.8, Module1.187 (MIPI1_C_N)
/CM5_HighSpeed/DPHY1_C_P: J16.9, Module1.189 (MIPI1_C_P)
/CM5_HighSpeed/DPHY1_D0_N: J16.2, Module1.175 (MIPI1_D0_N)
/CM5_HighSpeed/DPHY1_D0_P: J16.3, Module1.177 (MIPI1_D0_P)
/CM5_HighSpeed/DPHY1_D1_N: J16.5, Module1.181 (MIPI1_D1_N)
/CM5_HighSpeed/DPHY1_D1_P: J16.6, Module1.183 (MIPI1_D1_P)
/CM5_HighSpeed/DPHY1_D2_N: J16.11, Module1.193 (MIPI1_D2_N)
/CM5_HighSpeed/DPHY1_D2_P: J16.12, Module1.195 (MIPI1_D2_P)
/CM5_HighSpeed/DPHY1_D3_N: J16.14, Module1.194 (MIPI1_D3_N)
/CM5_HighSpeed/DPHY1_D3_P: J16.15, Module1.196 (MIPI1_D3_P)
/CM5_HighSpeed/HDMI0_CEC: J22.15 (CEC), Module1.151 (HDMI0_CEC)
/CM5_HighSpeed/HDMI0_CK_N: J22.14 (CK-), Module1.190 (HDMI0_CLK_N)
/CM5_HighSpeed/HDMI0_CK_P: J22.12 (CK+), Module1.188 (HDMI0_CLK_P)
/CM5_HighSpeed/HDMI0_D0_N: J22.11 (D0-), Module1.184 (HDMI0_TX0_N)
/CM5_HighSpeed/HDMI0_D0_P: J22.9 (D0+), Module1.182 (HDMI0_TX0_P)
/CM5_HighSpeed/HDMI0_D1_N: J22.8 (D1-), Module1.178 (HDMI0_TX1_N)
/CM5_HighSpeed/HDMI0_D1_P: J22.6 (D1+), Module1.176 (HDMI0_TX1_P)
/CM5_HighSpeed/HDMI0_D2_N: J22.5 (D2-), Module1.172 (HDMI0_TX2_N)
/CM5_HighSpeed/HDMI0_D2_P: J22.3 (D2+), Module1.170 (HDMI0_TX2_P)
/CM5_HighSpeed/HDMI0_HOTPLUG: J22.1 (HPD/HEAC-), Module1.153 (HDMI0_HOTPLUG)
/CM5_HighSpeed/HDMI0_SCL: J22.17 (SCL), Module1.200 (HDMI0_SCL)
/CM5_HighSpeed/HDMI0_SDA: J22.18 (SDA), Module1.199 (HDMI0_SDA)
/CM5_HighSpeed/HDMI_5v: C13.1, J22.19 (+5V), TP10.1, U12.2 (OUT)
/CM5_HighSpeed/PCIE_CLKREQ_N: J3.15, Module1.102 (PCIe_nCLKREQ)
/CM5_HighSpeed/PCIE_CLK_N: J3.5, Module1.112 (PCIe_CLK_N)
/CM5_HighSpeed/PCIE_CLK_P: J3.4, Module1.110 (PCIe_CLK_P)
/CM5_HighSpeed/PCIE_DET_WAKE: J3.14, Module1.104 (PCIE_nWAKE)
/CM5_HighSpeed/PCIE_PWR_EN: J3.13, Module1.106 (PCIE_PWR_EN)
/CM5_HighSpeed/PCIE_RST_B: J3.16, Module1.109 (PCIe_nRST)
/CM5_HighSpeed/PCIE_RX_N: J3.8, Module1.118 (PCIe_RX_N)
/CM5_HighSpeed/PCIE_RX_P: J3.7, Module1.116 (PCIe_RX_P)
/CM5_HighSpeed/PCIE_TX_N: J3.11, Module1.124 (PCIe_TX_N)
/CM5_HighSpeed/PCIE_TX_P: J3.10, Module1.122 (PCIe_TX_P)
/CM5_HighSpeed/SCL0: J5.20; also elsewhere on the board
/CM5_HighSpeed/SCL1: J16.20, R7.2; also elsewhere on the board
/CM5_HighSpeed/SDA0: J5.21; also elsewhere on the board
/CM5_HighSpeed/SDA1: J16.21, R6.2; also elsewhere on the board
/CM5_HighSpeed/USB3-0-D_N: J12.2 (D-), Module1.136 (USB3-0-D_N)
/CM5_HighSpeed/USB3-0-D_P: J12.3 (D+), Module1.134 (USB3-0-D_P)
/CM5_HighSpeed/USB3-0-RX_N: J12.5 (SSRX-), Module1.128 (USB3-0-RX_N)
/CM5_HighSpeed/USB3-0-RX_P: J12.6 (SSRX+), Module1.130 (USB3-0-RX_P)
/CM5_HighSpeed/USB3-0-TX_N: J12.8 (SSTX-), Module1.140 (USB3-0-TX_N)
/CM5_HighSpeed/USB3-0-TX_P: J12.9 (SSTX+), Module1.142 (USB3-0-TX_P)
/CM5_HighSpeed/VBUS: C3.1, C7.1, C8.1, J12.1 (VBUS), TP9.1, U6.6 (OUT)
/CM5_HighSpeed/VBUS_EN: Module1.111 (VBUS_EN), U6.3 (EN)
/USB2_N: Module1.103 (USB2_N); also elsewhere on the board
/USB2_P: Module1.105 (USB2_P); also elsewhere on the board
GND: C2.2, C3.2, C7.2, C8.2, C12.2, C13.2, J3.3, J3.6, J3.9, J3.12, J3.SH1, J3.SH2, J3.SH3, J3.SH4, J5.1, J5.4, J5.7, J5.10, J5.13, J5.16, J5.19, J12.4 (GND), J12.7 (DRAIN), J12.10 (SHIELD), J16.1, J16.4, J16.7, J16.10, J16.13, J16.16, J16.19, J22.4 (D2S), J22.7 (D1S), J22.10 (D0S), J22.13 (CKS), J22.16 (GND), J22.SH, Module1.107 (GND), Module1.108 (GND), Module1.113 (GND), Module1.114 (GND), Module1.119 (GND), Module1.120 (GND), Module1.125 (GND), Module1.126 (GND), Module1.131 (GND), Module1.132 (GND), Module1.137 (GND), Module1.138 (GND), Module1.144 (GND), Module1.150 (GND), Module1.155 (GND), Module1.156 (GND), Module1.161 (GND), Module1.162 (GND), Module1.167 (GND), Module1.168 (GND), Module1.173 (GND), Module1.174 (GND), Module1.179 (GND), Module1.180 (GND), Module1.185 (GND), Module1.186 (GND), Module1.191 (GND), Module1.192 (GND), Module1.197 (GND), Module1.198 (GND), R12.2, U6.2 (GND), U12.3 (GND); also elsewhere on the board
unnamed: J16.17, R8.2
unnamed: R12.1, U6.5 (ILIM)

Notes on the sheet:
USB 3 Pairs P/N swapped to help routing
Current Limit switch
DSI/CSI Connectors
Originally 6.3V tantalum. Use 10V to be sure.

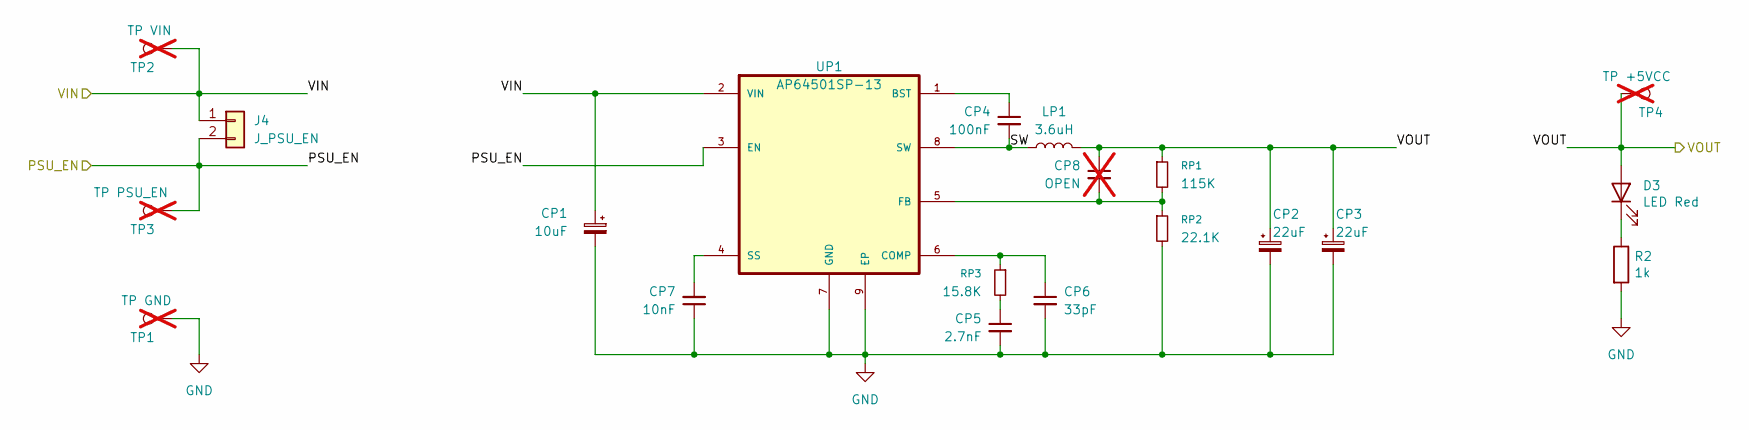
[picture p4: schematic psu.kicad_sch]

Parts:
CP1: 10uF; CP_EIA-6032-28_Kemet-C_HandSolder
CP2, CP3: 22uF; CP_EIA-3528-21_Kemet-B_HandSolder
CP4: 100nF; C_0805_2012Metric_Pad1.18x1.45mm_HandSolder
CP5: 2.7nF; C_0805_2012Metric_Pad1.18x1.45mm_HandSolder
CP6: 33pF; C_0805_2012Metric_Pad1.18x1.45mm_HandSolder
CP7: 10nF; C_0805_2012Metric_Pad1.18x1.45mm_HandSolder
CP8: OPEN; C_0805_2012Metric_Pad1.18x1.45mm_HandSolder; not fitted
D3: LED Red; LED_0603_1608Metric; Part Description Red 620nm LED Indication - Discrete 2.2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
J4: J_PSU_EN; PinHeader_1x02_P2.54mm_Vertical
LP1: 3.6uH; L_Bourns-SRN8040_8x8.15mm
R2: 1k; R_0402_1005Metric; Part Description Resistor 1K M1005 1% 63mW
RP1: 115K; R_0805_2012Metric_Pad1.20x1.40mm_HandSolder
RP2: 22.1K; R_0805_2012Metric_Pad1.20x1.40mm_HandSolder
RP3: 15.8K; R_0805_2012Metric_Pad1.20x1.40mm_HandSolder
TP1: TP GND; TestPoint_Pad_2.0x2.0mm; Part Description Test point; not fitted
TP2: TP VIN; TestPoint_Pad_2.0x2.0mm; Part Description Test point; not fitted
TP3: TP PSU_EN; TestPoint_Pad_2.0x2.0mm; Part Description Test point; not fitted
TP4: TP +5VCC; TestPoint_Pad_2.0x2.0mm; Part Description Test point; not fitted
UP1: AP64501SP-13; SOP_AP64501SP-13_DIO

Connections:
/+5v: CP2.1, CP3.1, CP8.1, D3.2 (A), LP1.2, RP1.1, TP4.1; also elsewhere on the board
/PSU/PSU_EN: J4.2, TP3.1, UP1.3 (EN)
/PSU/SW: CP4.2, LP1.1, UP1.8 (SW)
/VIN: CP1.1, J4.1, TP2.1, UP1.2 (VIN); also elsewhere on the board
GND: CP1.2, CP2.2, CP3.2, CP5.2, CP6.2, CP7.1, R2.2, RP2.2, TP1.1, UP1.7 (GND), UP1.9 (EP); also elsewhere on the board
unnamed: CP5.1, RP3.2
unnamed: D3.1 (K), R2.1
unnamed: CP4.1, UP1.1 (BST)
unnamed: CP6.1, RP3.1, UP1.6 (COMP)
unnamed: CP8.2, RP1.2, RP2.1, UP1.5 (FB)
unnamed: CP7.2, UP1.4 (SS)

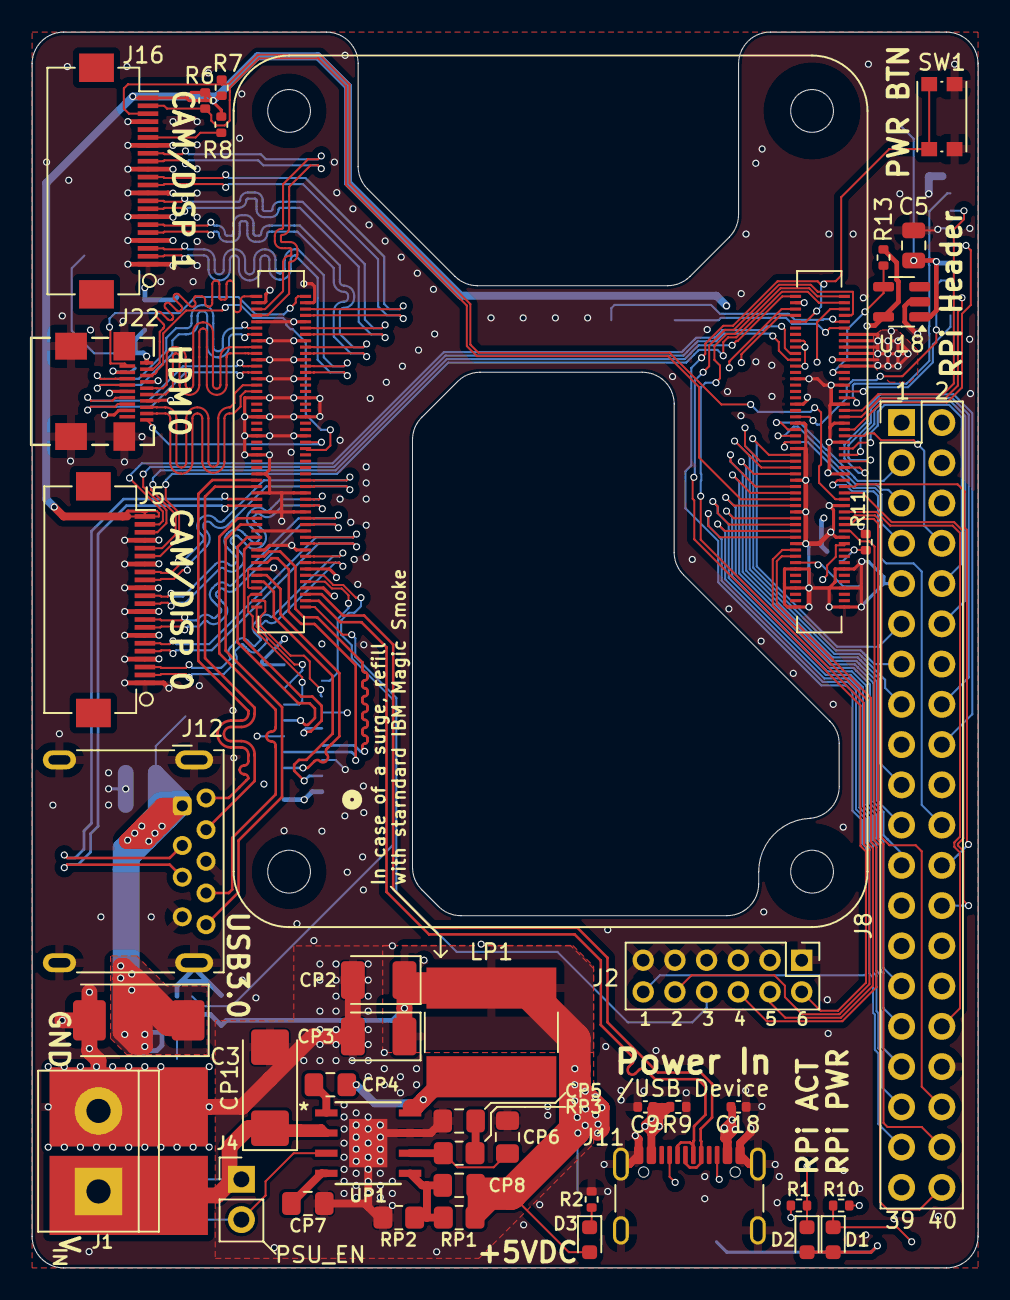
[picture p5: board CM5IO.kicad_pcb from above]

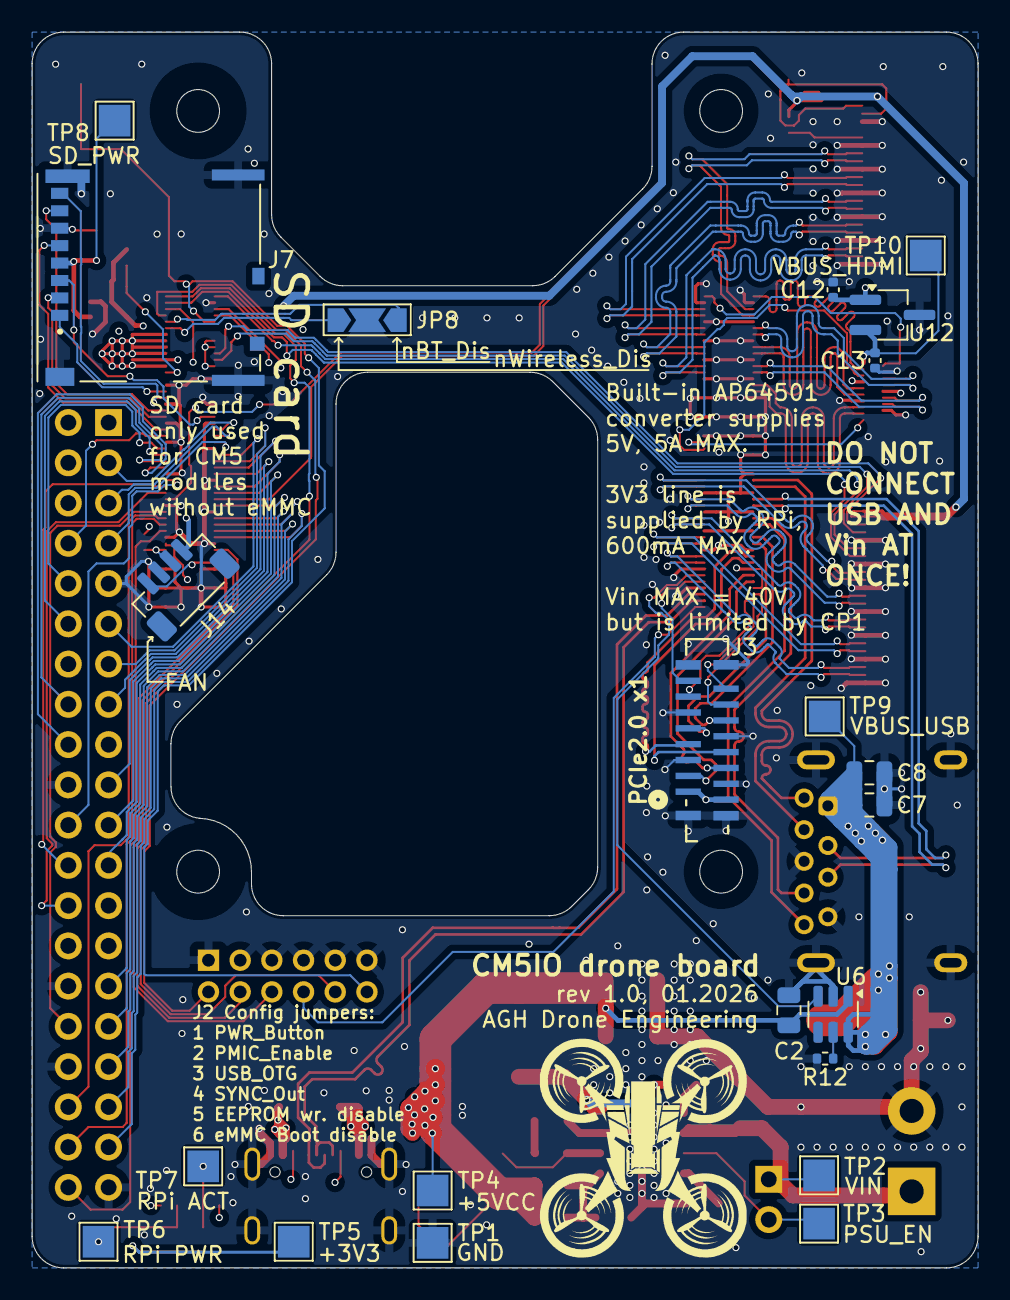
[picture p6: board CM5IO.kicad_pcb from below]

Board: 4 copper layers, 59.7 x 78.0 mm, 65 parts (22 on the bottom side), 123 nets.

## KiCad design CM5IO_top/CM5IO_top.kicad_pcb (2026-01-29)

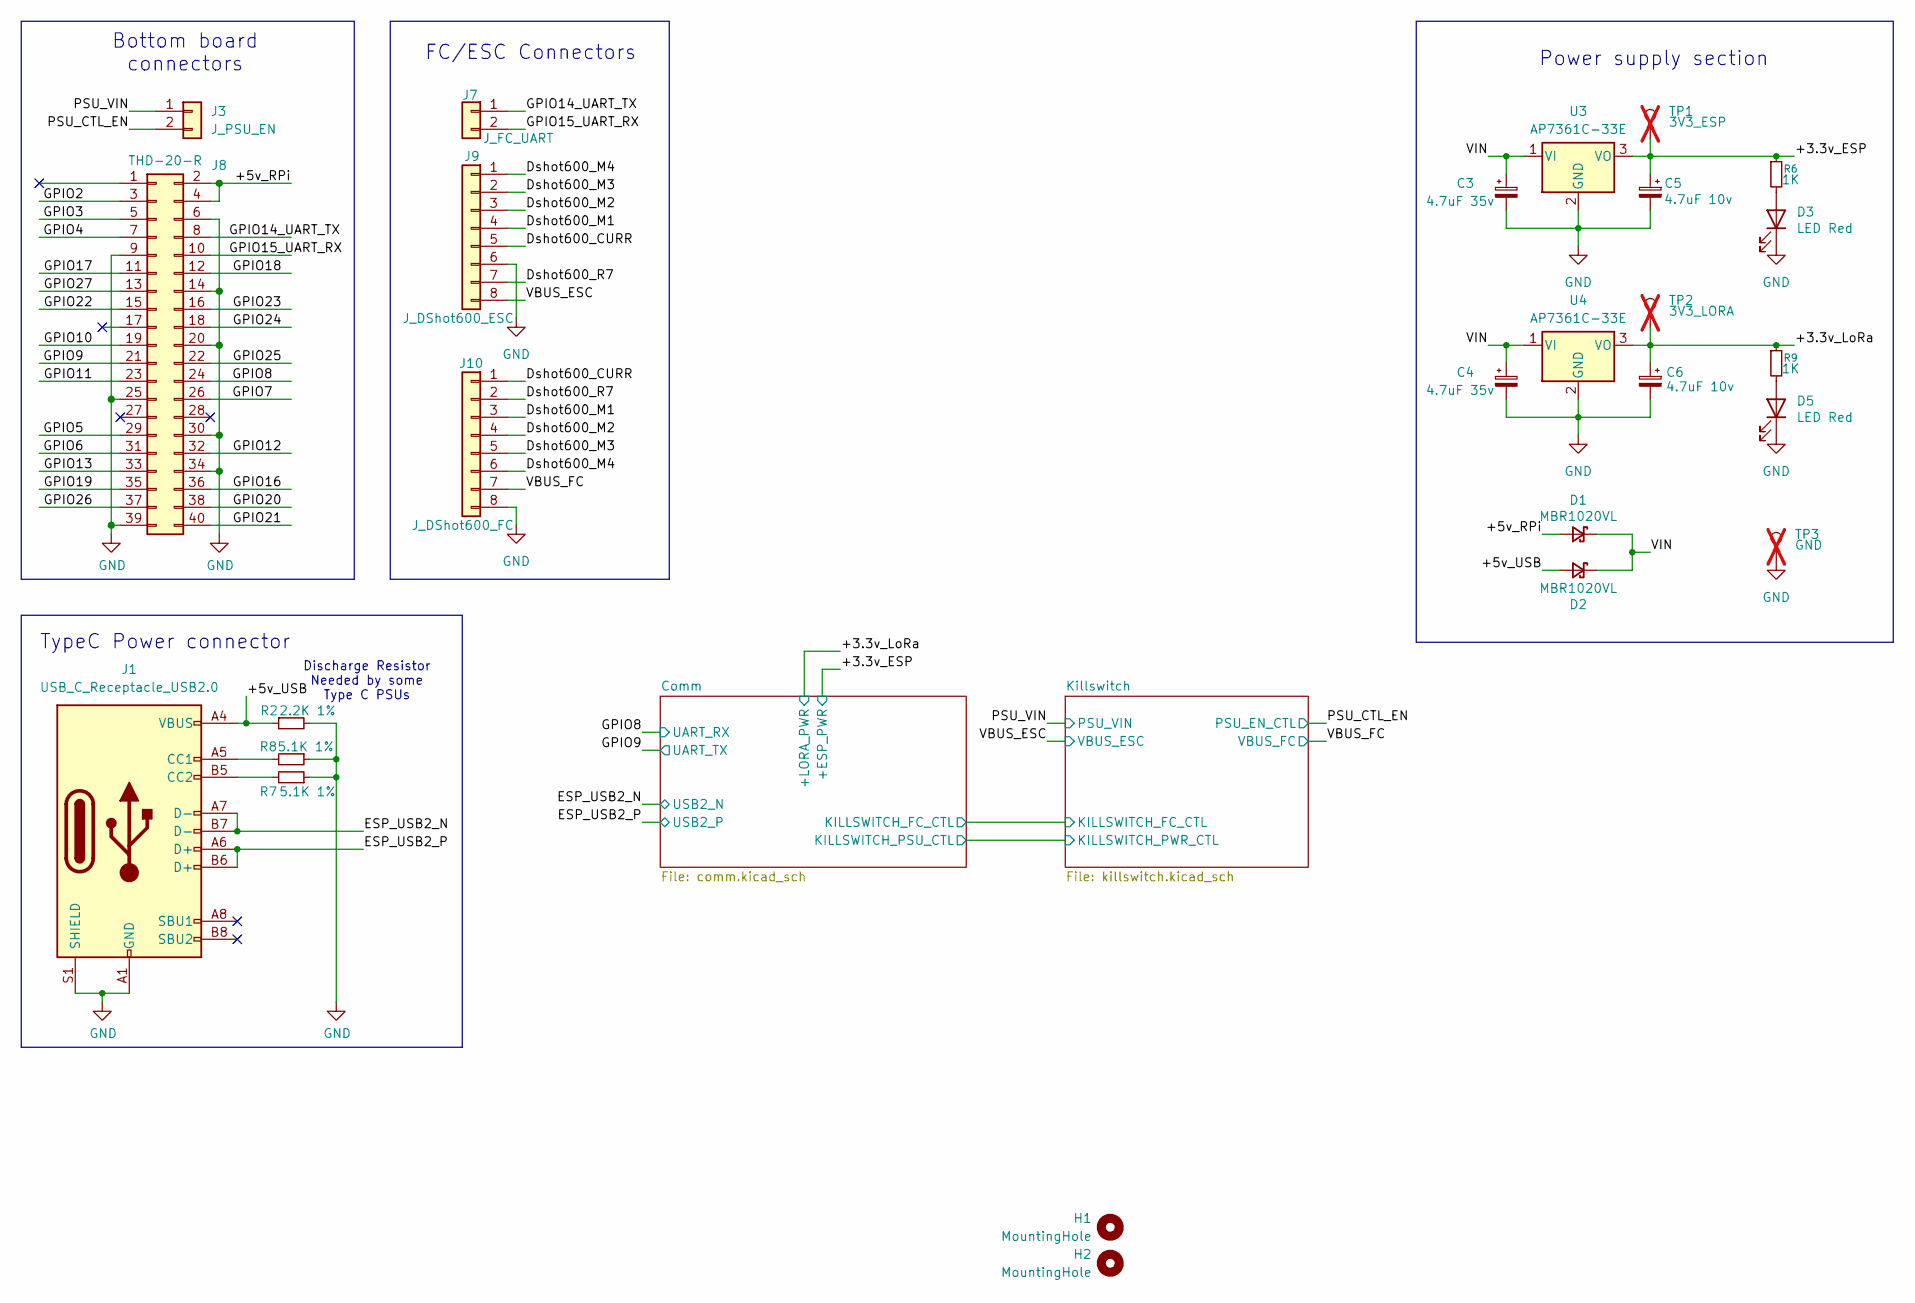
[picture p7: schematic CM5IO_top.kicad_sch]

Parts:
C3, C4: 4.7uF 35v; CP_EIA-3528-21_Kemet-B_HandSolder
C5, C6: 4.7uF 10v; CP_EIA-3216-18_Kemet-A_HandSolder
D1, D2: MBR1020VL; D_SOD-123F
D3, D5: LED Red; LED_0603_1608Metric; Part Description Red 620nm LED Indication - Discrete 2.2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
H1, H2: MountingHole; MountingHole_2.7mm_M2.5_DIN965
J1: USB_C_Receptacle_USB2.0; USB_C_Receptacle_GCT_USB4105-xx-A_16P_TopMnt_Horizontal; Part Description USBC USB2 data and power connector
J3: J_PSU_EN; PinSocket_1x02_P2.54mm_Vertical_SMD_Pin1Left
J7: J_FC_UART; Molex_PicoBlade_53048-0210_1x02_P1.25mm_Horizontal; Part Description Pin Header, Right Angle, Signal, 1.25 m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
J8: THD-20-R; PinSocket_2x20_P2.54mm_Vertical; Part Description PinHeader_2x20_P2.54mm_Vertical
J9: J_DShot600_ESC; Molex_PicoBlade_53048-0810_1x08_P1.25mm_Horizontal; Part Description Pin Header, Right Angle, Signal, 1.25 m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
J10: J_DShot600_FC; Molex_PicoBlade_53048-0810_1x08_P1.25mm_Horizontal; Part Description Pin Header, Right Angle, Signal, 1.25 m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
R2: 2.2K 1%; R_0805_2012Metric_Pad1.20x1.40mm_HandSolder; Part Description Resistor 2.2K 1% 63mW
R6, R9: 1K; R_0805_2012Metric_Pad1.20x1.40mm_HandSolder
R7, R8: 5.1K 1%; R_0805_2012Metric_Pad1.20x1.40mm_HandSolder; Part Description Resistor 5.1K 1% 63mW
TP1: 3V3_ESP; TestPoint_Pad_2.0x2.0mm; Part Description Test point; not fitted
TP2: 3V3_LORA; TestPoint_Pad_2.0x2.0mm; Part Description Test point; not fitted
TP3: GND; TestPoint_Pad_2.0x2.0mm; Part Description Test point; not fitted
U3, U4: AP7361C-33E; SOT-223-3_TabPin2; Part Description LDO, FIXED, 3.3V, 1A, -40 TO 85DEG C

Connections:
/+3.3v_ESP: C5.1, R6.1, TP1.1, U3.3 (VO); also elsewhere on the board
/+3.3v_LoRa: C6.1, R9.1, TP2.1, U4.3 (VO); also elsewhere on the board
/+5v_RPi: D1.2 (A), J8.2, J8.4
/+5v_USB: D2.2 (A), J1.A4 (VBUS), J1.A9 (VBUS), J1.B4 (VBUS), J1.B9 (VBUS), R2.1
/Dshot600_CURR: J9.5, J10.1
/Dshot600_M1: J9.4, J10.3
/Dshot600_M2: J9.3, J10.4
/Dshot600_M3: J9.2, J10.5
/Dshot600_M4: J9.1, J10.6
/Dshot600_R7: J9.7, J10.2
/ESP_USB2_N: J1.A7 (D-), J1.B7 (D-); also elsewhere on the board
/ESP_USB2_P: J1.A6 (D+), J1.B6 (D+); also elsewhere on the board
/GPIO2: J8.3
/GPIO3: J8.5
/GPIO4: J8.7
/GPIO5: J8.29
/GPIO6: J8.31
/GPIO7: J8.26
/GPIO8: J8.24; also elsewhere on the board
/GPIO9: J8.21; also elsewhere on the board
/GPIO10: J8.19
/GPIO11: J8.23
/GPIO12: J8.32
/GPIO13: J8.33
/GPIO14_UART_TX: J7.1, J8.8
/GPIO15_UART_RX: J7.2, J8.10
/GPIO16: J8.36
/GPIO17: J8.11
/GPIO18: J8.12
/GPIO19: J8.35
/GPIO20: J8.38
/GPIO21: J8.40
/GPIO22: J8.15
/GPIO23: J8.16
/GPIO24: J8.18
/GPIO25: J8.22
/GPIO26: J8.37
/GPIO27: J8.13
/PSU_CTL_EN: J3.2; also elsewhere on the board
/PSU_VIN: J3.1; also elsewhere on the board
/VBUS_ESC: J9.8; also elsewhere on the board
/VBUS_FC: J10.7; also elsewhere on the board
/VIN: C3.1, C4.1, D1.1 (K), D2.1 (K), U3.1 (VI), U4.1 (VI)
GND: C3.2, C4.2, C5.2, C6.2, D3.1 (K), D5.1 (K), J1.A1 (GND), J1.A12 (GND), J1.B1 (GND), J1.B12 (GND), J1.S1 (SHIELD), J8.6, J8.9, J8.14, J8.20, J8.25, J8.30, J8.34, J8.39, J9.6, J10.8, R2.2, R7.1, R8.1, TP3.1, U3.2 (GND), U4.2 (GND); also elsewhere on the board
unnamed: D3.2 (A), R6.2
unnamed: D5.2 (A), R9.2
unnamed: J1.A5 (CC1), R8.2
unnamed: J1.B5 (CC2), R7.2

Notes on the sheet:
Discharge Resistor Needed by some Type C PSUs
FC/ESC Connectors
Power supply section
TypeC Power connector
Bottom board connectors

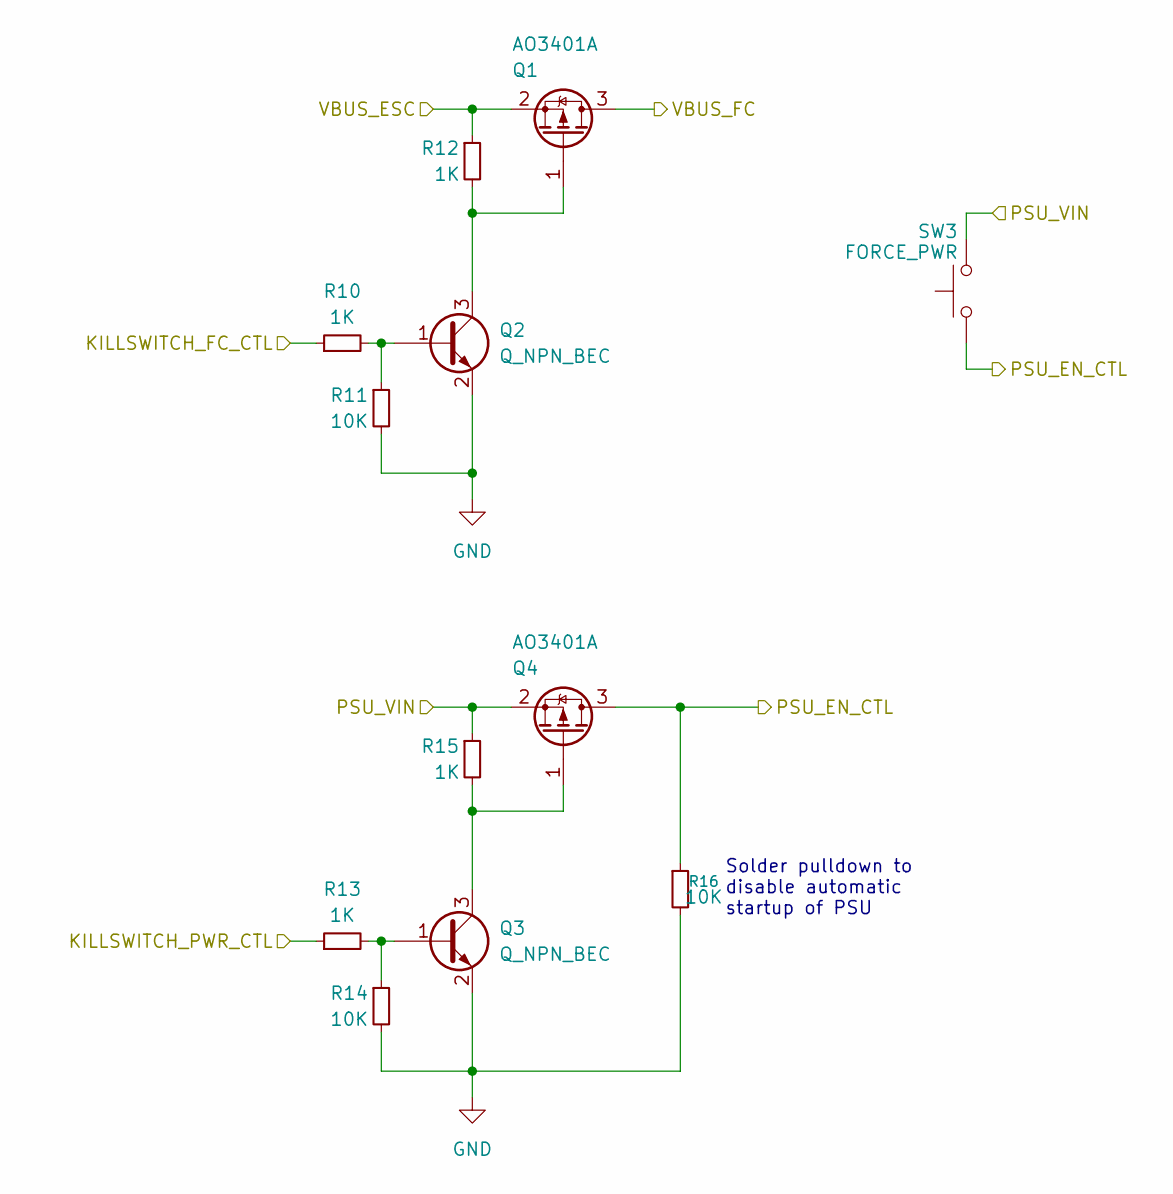
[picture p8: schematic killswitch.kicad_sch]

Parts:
Q1, Q4: AO3401A; SOT-23
Q2, Q3: Q_NPN_BEC; SOT-23
R10, R12, R13, R15: 1K; R_0805_2012Metric_Pad1.20x1.40mm_HandSolder
R11, R14, R16: 10K; R_0805_2012Metric_Pad1.20x1.40mm_HandSolder
SW3: FORCE_PWR; SW_Push_1P1T_NO_CK_KMR2; Part Description Tactile Switch, KMR 2 Series, Top Actua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

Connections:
/Comm/KILLSWITCH_FC_CTL: R10.1; also elsewhere on the board
/Comm/KILLSWITCH_PSU_CTL: R13.1; also elsewhere on the board
/PSU_CTL_EN: Q4.3 (D), R16.1, SW3.1; also elsewhere on the board
/PSU_VIN: Q4.2 (S), R15.1, SW3.2; also elsewhere on the board
/VBUS_ESC: Q1.2 (S), R12.1; also elsewhere on the board
/VBUS_FC: Q1.3 (D); also elsewhere on the board
GND: Q2.2 (E), Q3.2 (E), R11.2, R14.2, R16.2; also elsewhere on the board
unnamed: Q1.1 (G), Q2.3 (C), R12.2
unnamed: Q2.1 (B), R10.2, R11.1
unnamed: Q3.1 (B), R13.2, R14.1
unnamed: Q3.3 (C), Q4.1 (G), R15.2

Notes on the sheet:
Solder pulldown to disable automatic startup of PSU

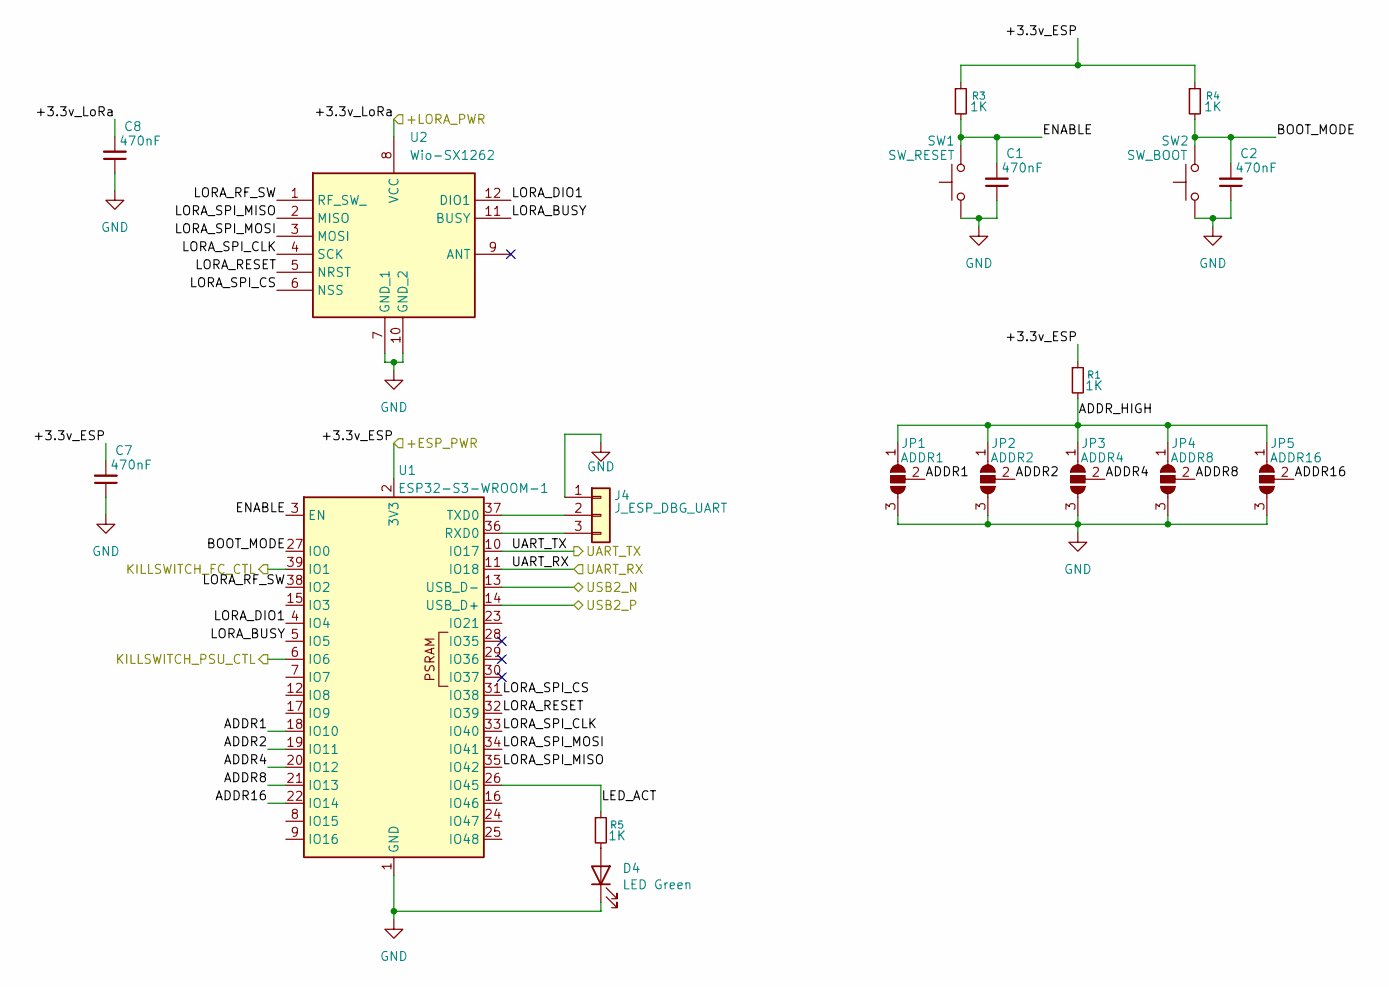
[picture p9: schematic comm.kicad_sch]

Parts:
C1, C2, C7, C8: 470nF; C_0805_2012Metric_Pad1.18x1.45mm_HandSolder
D4: LED Green; LED_0603_1608Metric; Part Description Green 572nm LED Indication - Discrete 2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
J4: J_ESP_DBG_UART; Molex_PicoBlade_53047-0310_1x03_P1.25mm_Vertical; Part Description Pin Header, Vertical, Signal, Wire-to-B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
JP1: ADDR1; SolderJumper-3_P2.0mm_Open_TrianglePad1.0x1.5mm
JP2: ADDR2; SolderJumper-3_P2.0mm_Open_TrianglePad1.0x1.5mm
JP3: ADDR4; SolderJumper-3_P2.0mm_Open_TrianglePad1.0x1.5mm
JP4: ADDR8; SolderJumper-3_P2.0mm_Open_TrianglePad1.0x1.5mm
JP5: ADDR16; SolderJumper-3_P2.0mm_Open_TrianglePad1.0x1.5mm
R1, R3, R4, R5: 1K; R_0805_2012Metric_Pad1.20x1.40mm_HandSolder
SW1: SW_RESET; SW_Push_1P1T_NO_CK_KMR2; Part Description Tactile Switch, KMR 2 Series, Top Actua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
SW2: SW_BOOT; SW_Push_1P1T_NO_CK_KMR2; Part Description Tactile Switch, KMR 2 Series, Top Actua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
U1: ESP32-S3-WROOM-1; ESP32-S3-WROOM-1U
U2: Wio-SX1262; Mouser Part Number 713-114993390

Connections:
/+3.3v_ESP: C7.2, R1.1, R3.1, R4.1, U1.2 (3V3); also elsewhere on the board
/+3.3v_LoRa: C8.2, U2.8 (VCC); also elsewhere on the board
/Comm/ADDR1: JP1.2 (C), U1.18 (IO10)
/Comm/ADDR2: JP2.2 (C), U1.19 (IO11)
/Comm/ADDR4: JP3.2 (C), U1.20 (IO12)
/Comm/ADDR8: JP4.2 (C), U1.21 (IO13)
/Comm/ADDR16: JP5.2 (C), U1.22 (IO14)
/Comm/ADDR_HIGH: JP1.1 (A), JP2.1 (A), JP3.1 (A), JP4.1 (A), JP5.1 (A), R1.2
/Comm/BOOT_MODE: C2.2, R4.2, SW2.2, U1.27 (IO0)
/Comm/ENABLE: C1.2, R3.2, SW1.2, U1.3 (EN)
/Comm/KILLSWITCH_FC_CTL: U1.39 (IO1); also elsewhere on the board
/Comm/KILLSWITCH_PSU_CTL: U1.6 (IO6); also elsewhere on the board
/Comm/LED_ACT: R5.1, U1.26 (IO45)
/Comm/LORA_BUSY: U1.5 (IO5), U2.11 (BUSY)
/Comm/LORA_DIO1: U1.4 (IO4), U2.12 (DIO1)
/Comm/LORA_RESET: U1.32 (IO39), U2.5 (NRST)
/Comm/LORA_RF_SW: U1.38 (IO2), U2.1 (RF_SW_)
/Comm/LORA_SPI_CLK: U1.33 (IO40), U2.4 (SCK)
/Comm/LORA_SPI_CS: U1.31 (IO38), U2.6 (NSS)
/Comm/LORA_SPI_MISO: U1.35 (IO42), U2.2 (MISO)
/Comm/LORA_SPI_MOSI: U1.34 (IO41), U2.3 (MOSI)
/ESP_USB2_N: U1.13 (USB_D-); also elsewhere on the board
/ESP_USB2_P: U1.14 (USB_D+); also elsewhere on the board
/GPIO8: U1.11 (IO18); also elsewhere on the board
/GPIO9: U1.10 (IO17); also elsewhere on the board
GND: C1.1, C2.1, C7.1, C8.1, D4.1 (K), J4.1, JP1.3 (B), JP2.3 (B), JP3.3 (B), JP4.3 (B), JP5.3 (B), SW1.1, SW2.1, U1.1 (GND), U1.40 (GND), U1.41 (GND), U2.7 (GND_1), U2.10 (GND_2); also elsewhere on the board
unnamed: D4.2 (A), R5.2
unnamed: J4.2, U1.37 (TXD0)
unnamed: J4.3, U1.36 (RXD0)

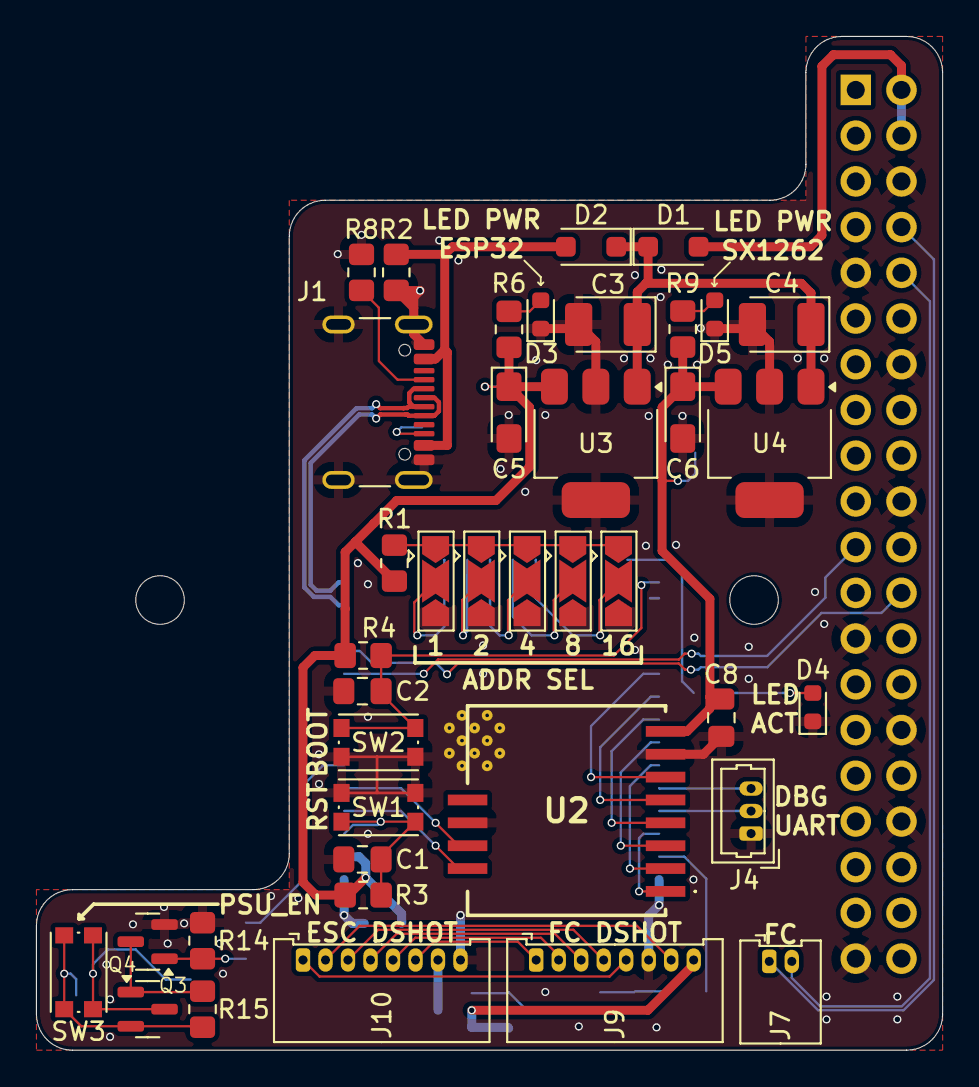
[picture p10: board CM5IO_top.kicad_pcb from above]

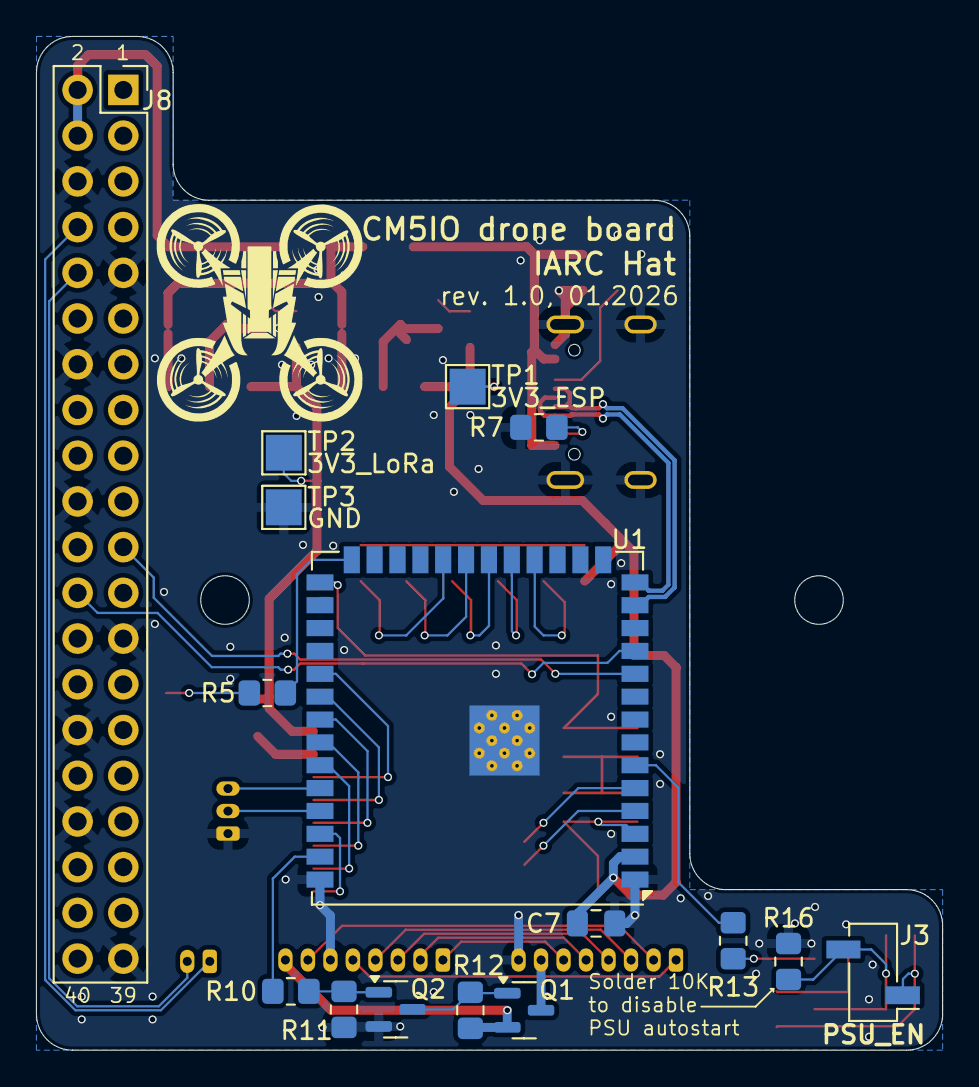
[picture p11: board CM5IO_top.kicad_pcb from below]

Board: 2 copper layers, 50.3 x 56.3 mm, 58 parts (16 on the bottom side), 52 nets.

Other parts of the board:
Module1: ComputeModule5-CM5; Raspberry-Pi-5-Compute-Module

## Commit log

2026-01-16 move bottom board into CM5IO
    [CM5IO-B_Adhesive.gbr, CM5IO-B_Courtyard.gbr, CM5IO-B_Cu.gbr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]
2026-01-17 small fixes for ground planes, logo added, minor other changes
    [CM5IO.kicad_pcb]
2026-01-19 update impedance calcs
    [CM5IO.kicad_pcb]
2026-01-20 post-review fixes
    [CM5IO.kicad_pcb]
2026-01-20 regenerate gerber files
    [CM5IO-B_Adhesive.gbr, CM5IO-B_Courtyard.gbr, CM5IO-B_Cu.gbr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]
2026-01-20 add the fan connector back
2026-01-21 add upper board draft
    [CM5IO_top.kicad_pcb, CM5IO_top.kicad_sch, comm.kicad_sch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]
2026-01-22 post-reveiw fixes
    [CM5IO-B_Adhesive.gbr, CM5IO-B_Courtyard.gbr, CM5IO-B_Cu.gbr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]
2026-01-22 final changes before ordering the design
    [CM5IO-B_Adhesive.gbr, CM5IO-B_Courtyard.gbr, CM5IO-B_Cu.gbr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]
2026-01-22 redesigning upper board
    [CM5IO_top.kicad_pcb, CM5IO_top.kicad_sch, comm.kicad_sch]
2026-01-22 top board wip
    [CM5IO_top.kicad_pcb]
2026-01-27 DRC fixes after changing via size. fixed too small cap in PSU.
    [CM5IO-B_Adhesive.gbr, CM5IO-B_Courtyard.gbr, CM5IO-B_Cu.gbr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]
2026-01-27 add BOM
    [CM5IO_BOM.xlsx]
2026-01-28 Add PCIe connector. Fix some clearance violations.
    [CM5IO-B_Adhesive.gbr, CM5IO-B_Courtyard.gbr, CM5IO-B_Cu.gbr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]
2026-01-29 upper board finished (I hope)
    [CM5IO_top-B_Adhesive.gbr, CM5IO_top-B_Courtyard.gbr, CM5IO_top-B_Cu.gbr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]
2026-01-29 minor aesthetic changes
    [CM5IO-B_Adhesive.gbr, CM5IO-B_Courtyard.gbr, CM5IO-B_Cu.gbr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]

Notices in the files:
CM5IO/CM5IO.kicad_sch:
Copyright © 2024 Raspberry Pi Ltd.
